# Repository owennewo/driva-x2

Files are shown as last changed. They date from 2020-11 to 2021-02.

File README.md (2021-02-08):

# driva-x2
Experimental dual BLDC board for use with [SimpleFOC](https://simplefoc.com)

This board will cost about $200 for 5 units from JLCPCB. Include are [gerber zip](https://github.com/owennewo/driva-x2/blob/main/kicad/gerber/driva-x2.zip), [BOM](https://github.com/owennewo/driva-x2/blob/main/kicad/assembly/driva-x2-bom.csv) and [POS](https://github.com/owennewo/driva-x2/blob/main/kicad/assembly/driva-x2-all-pos.csv).  Designed in Kicad.  This is pre-alpha quality e.g. I'm uncertain how much of it will work.  I've tested v0.5 with motor and hall sensors on left motor and that worked.

 - dual motor drivers using 3x btn8982 or ixf0007s
 - each motor has hall and spi port (untested)
 - prog (swd, swdio), can (untested), usart and i2c (untested) ports
 - ubg-otg (utested and without 5v attached)
 - onboard mpu6050 for 6 axis imu

Note JLCPCB won't do through hole components therefore all power, motor, comms ports will need to be hand solder as will the 1000uF cap.  

The BOM and Pick/Place/POS file are here:
https://github.com/owennewo/driva-x2/tree/main/kicad/assembly 

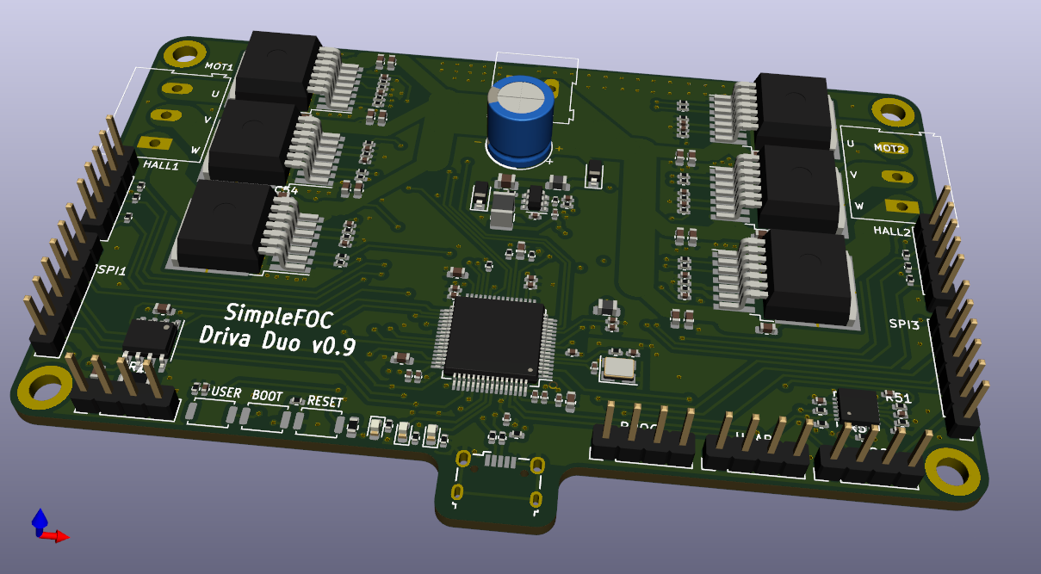
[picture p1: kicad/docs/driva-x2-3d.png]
3D render


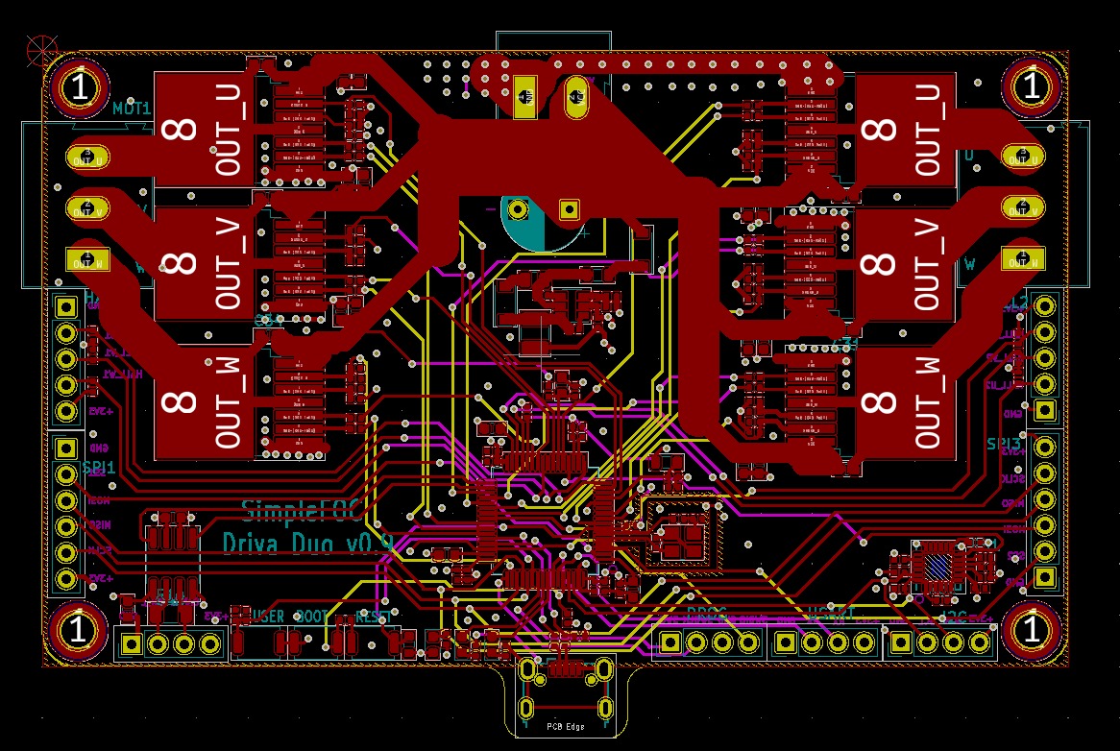
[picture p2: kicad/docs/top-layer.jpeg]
Top Layer


[PDF Schematic](./kicad/docs/driva-x2.pdf)

The gerber files are here:
https://github.com/owennewo/driva-x2/tree/main/kicad/gerber

The BOM and Pick/Place/POS file are here:
https://github.com/owennewo/driva-x2/tree/main/kicad/assembly

 * v0.5 - First attempt (partly working - problems with mpu6050, can and LDO)
 * v0.9 - Second attempt (fixed above hopefully - awaiting order from JLCPCB)

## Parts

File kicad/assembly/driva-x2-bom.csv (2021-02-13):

Id | Designator | Footprint | Quantity | Designation | LCSC Part Number
2 | C56,C54,C51,C49,C46,C44,C38,C36,C33,C31,C28,C26 | 0603 | 12 | 220n+ | C21120
3 | C55,C50,C45,C37,C32,C27 | 0603 | 6 | 100n+ | C14663
4 | R52,R51,R12,R13,R17,R21,R22,R25,R26,R29,R30,R33,R34,R37,R38,R41,R42 | 0402 | 17 | 10k | C25744
5 | R14 | 1206 | 1 | 120R+ | C22107
7 | R11 | 0603 | 1 | 2K2 | C4190
10 | C11,C2,C3,C4,C5,C6,C7,C8,C9,C10,C14,C18,C20,C25,C30,C35,C40,C41,C42,C48,C53,C58,C21 | 0402 | 23 | 100n | C1525
11 | C59 | 0402 | 1 | 33p | C1562
12 | C12 | 0402 | 1 | 10u | C15525
13 | U1 | SOT-23-6L | 1 | mp2451dt | C14123
14 | R50 | 0402 | 1 | 39k | C25783
15 | R49 | 0402 | 1 | 120k | C25750
16 | R48,R47,R46 | 0402 | 3 | 4.7k | C25900
17 | R45 | 0402 | 1 | 300K | C25774
18 | L1 | 1210 | 1 | 2.2uh | C86074
21 | D5,D1 | SOD-123 | 2 | b5819w | C8598
22 | C61,C15 | 0402 | 2 | 10n | C15195
23 | C13 | 0805 | 1 | 4.7u+ | C1779
24 | C1,C24 | 0603 | 2 | 10u | C19702
25 | C16,C17 | 0402 | 2 | 12p | C1547
26 | C19,C22,C23 | 0603 | 3 | 2.2u | C23630
27 | C29,C34,C39,C47,C52,C57 | 0402 | 6 | 1n | C1523
28 | C43 | 0402 | 1 | 2.2n | C1531
29 | D2 | LED_0603 | 1 | RED | C2286
30 | D3 | LED_0603 | 1 | GREEN | C72043
31 | D4 | LED_0603 | 1 | BLUE | C72041
32 | FB1,FB2 | 0805 | 2 | 100 @ 100Mhz | C1015
33 | HSE1 | SMD-CRY-3225_4P | 1 | 16MHz | C13738
42 | R1,R2,R3 | 0402 | 3 | 22R | C25092
43 | R4,R5,R6,R7,R8,R9 | 0402 | 6 | 1K5 | C25867
44 | R10 | 0402 | 1 | 220 | C25091
45 | R15 | 0402 | 1 | 33K | C25779
46 | R16 | 0402 | 1 | 3K3 | C25890
48 | R18,R19,R20,R23,R27,R31,R35,R39,R43 | 0402 | 9 | 1k | C11702
49 | R24,R28,R32,R36,R40,R44 | 0402 | 6 | 510R | C25123
50 | SW1,SW2,SW3 | SW-SMD-2_3.0x4.0x1.7 | 3 | push | C561519
51 | U2 | SOIC-8_3.9x4.9x1.27P | 1 | SN65HVD230 | C12084
52 | U3 | LQFP-64_10.0x10.0x0.5P | 1 | STM32F405RGTx | C15742
53 | U4,U5,U6,U8,U9,U10 | TO-263-7L | 6 | IFX007T | C74175
54 | U7 | QFN-24_EP_4.0x4.0x0.5P | 1 | MPU-6050 | C24112

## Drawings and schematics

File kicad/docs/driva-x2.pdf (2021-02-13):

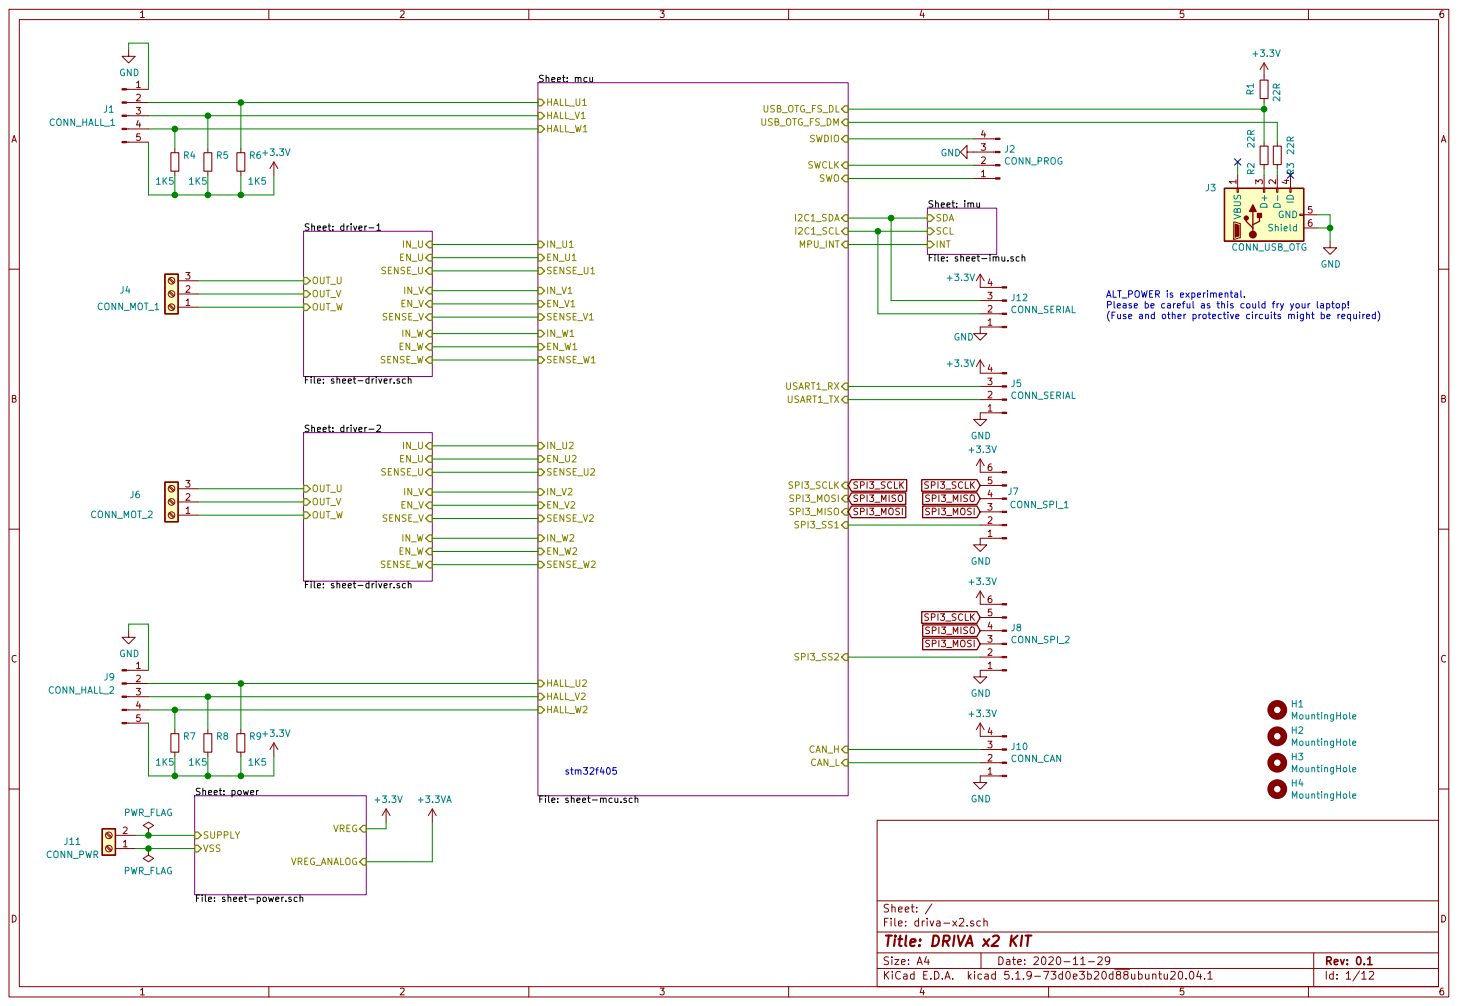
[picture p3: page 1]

Sheet: imu File: sheet-imu.sch SDA

INT Sheet: driver-1 File: sheet-driver.schSENSE_W

ALT_POWER is experimental.
Please be careful as this could fry your laptop!
(Fuse and other protective circuits might be required)
J10 CONN_CAN GND123456

Sheet: driver-2 File: sheet-driver.schSENSE_W

File: sheet-mcu.sch

File: sheet-power.sch VSS

File: driva-x2.sch Sheet: /
Id: 1/12 Title: DRIVA x2 KIT

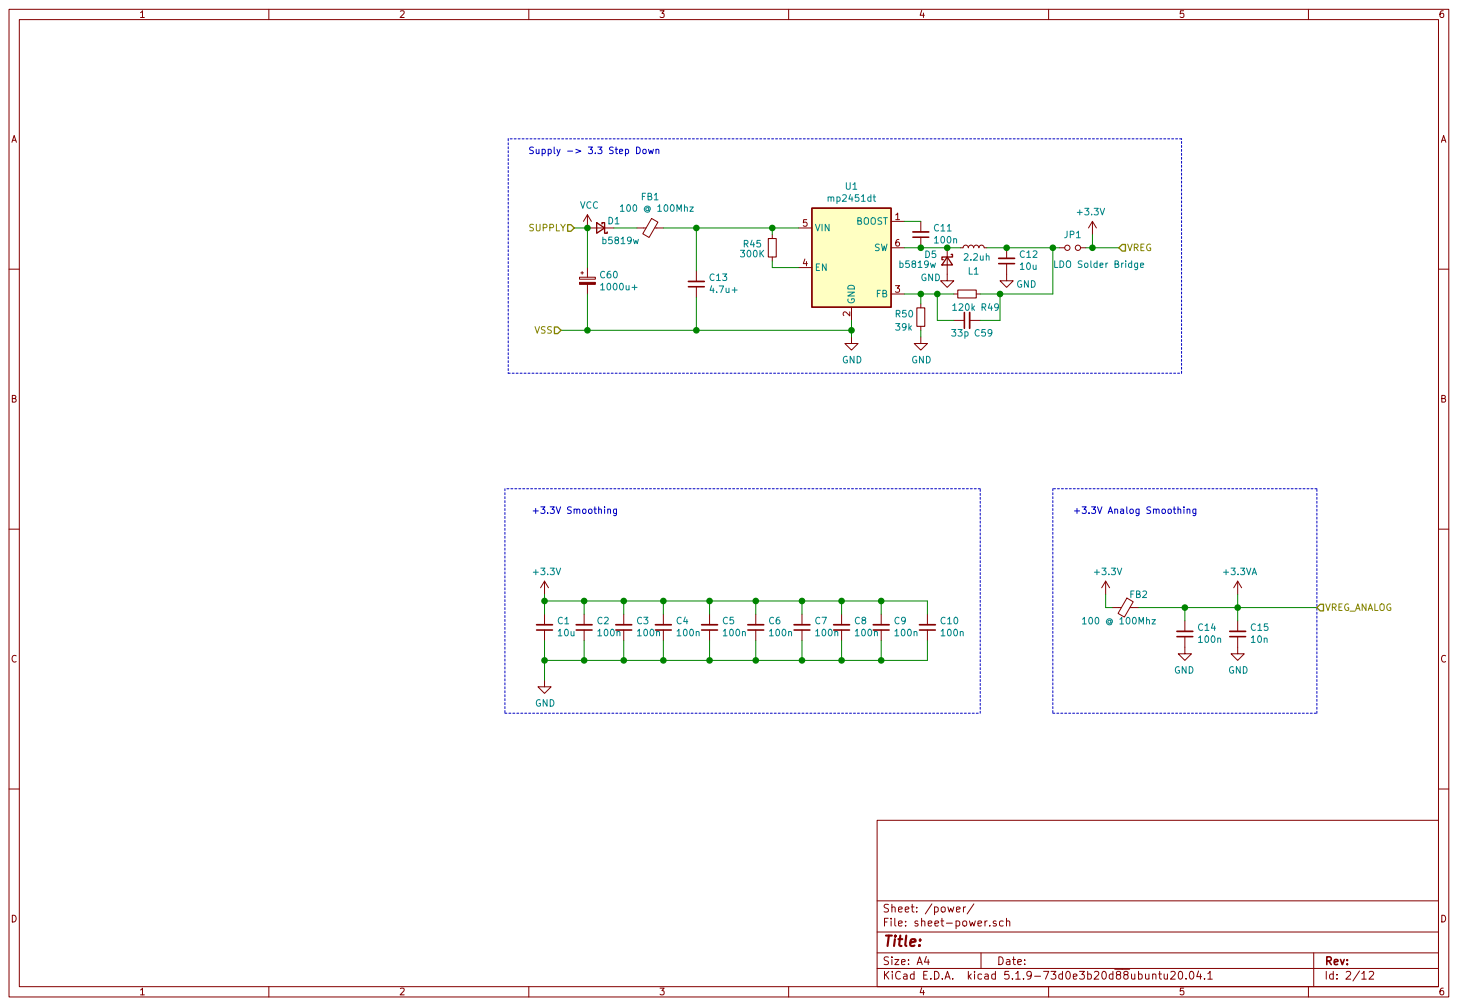
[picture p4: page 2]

2 FB 3 EN 4 VIN 5 SW 6 U1 mp2451dt GND GND

Sheet: /power/
File: sheet-power.sch
Id: 2/12 Title:

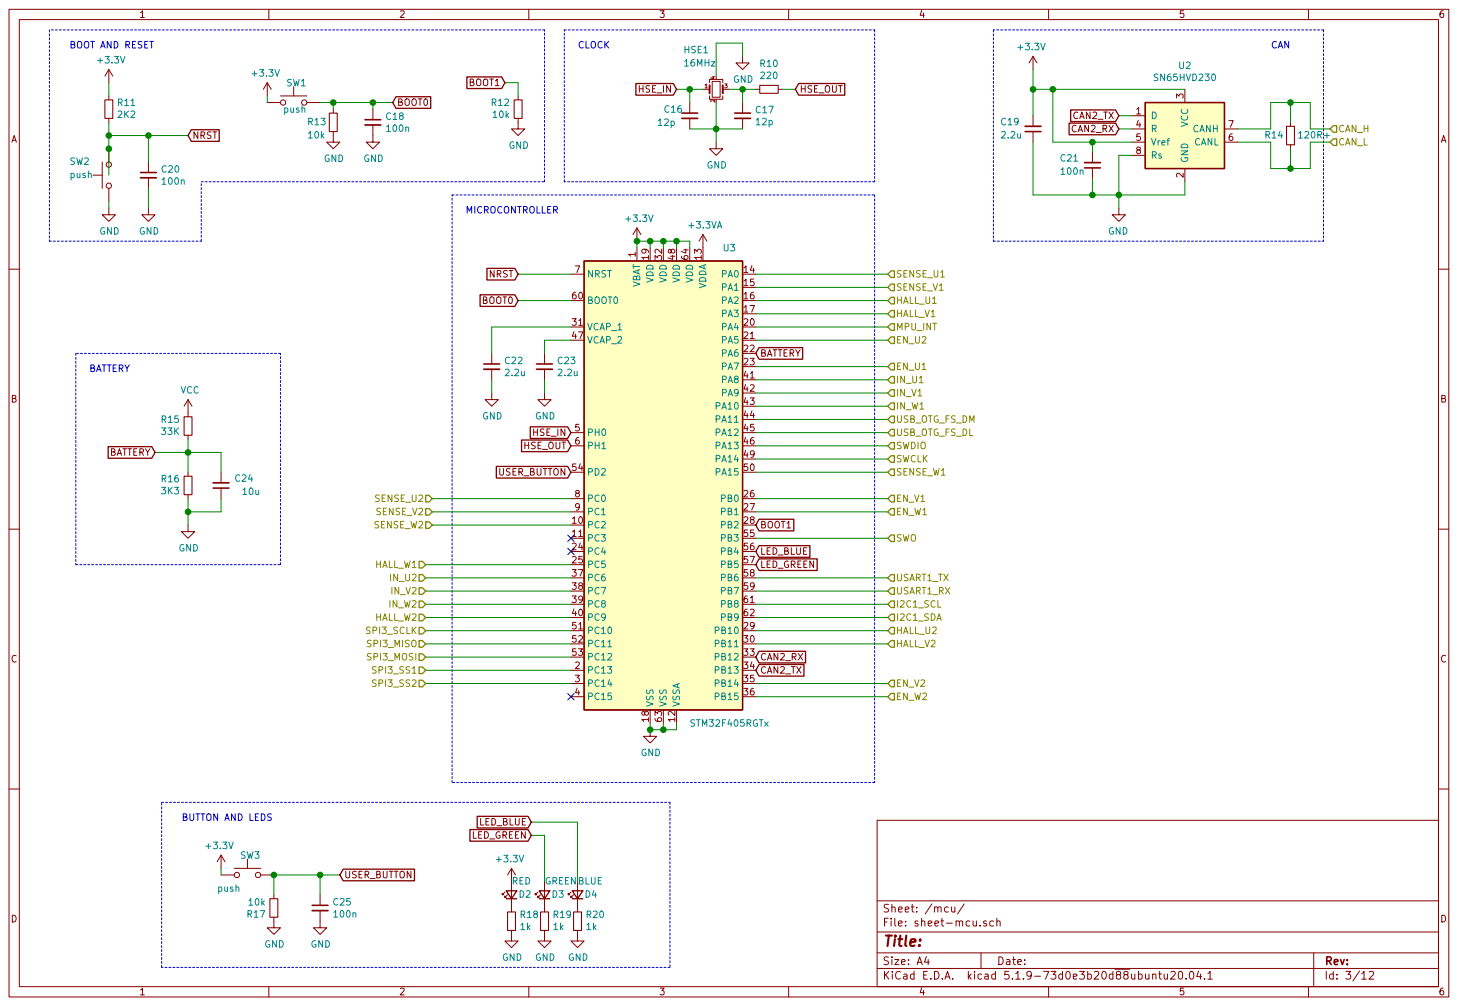
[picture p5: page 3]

1 VCAP_1 31 VCAP_2 47 VDD 19 VDD 32 VDD 48 VDD 64 VDDA 13 VSS 18 VSS 63 VSSA 12 U3 STM32F405RGTx

Id: 3/12 Title: File: sheet-mcu.sch Sheet: /mcu/ GND
1k GND

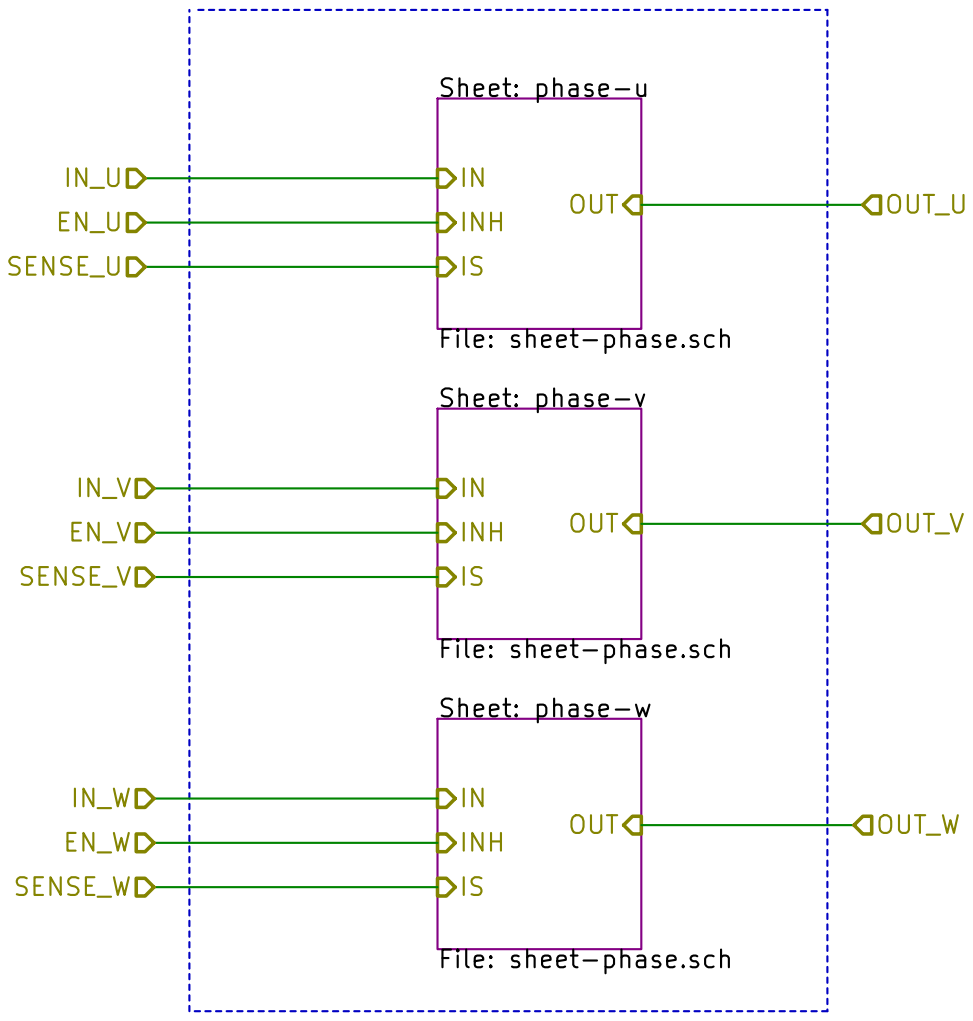
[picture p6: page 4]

File: sheet-phase.sch OUT
INH

Id: 4/12 Title: Driver File: sheet-driver.sch Sheet: /driver-2/ Root Top level

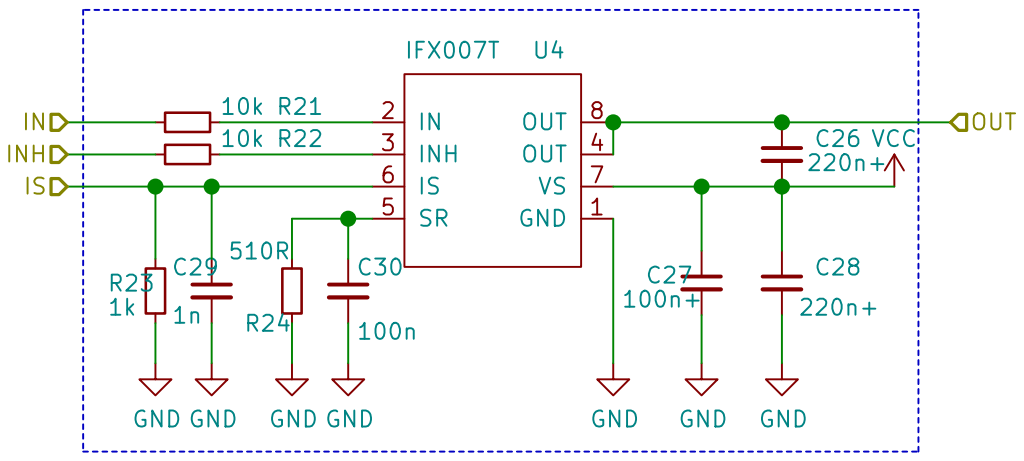
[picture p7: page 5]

File: sheet-phase.sch
Id: 5/12 Title:

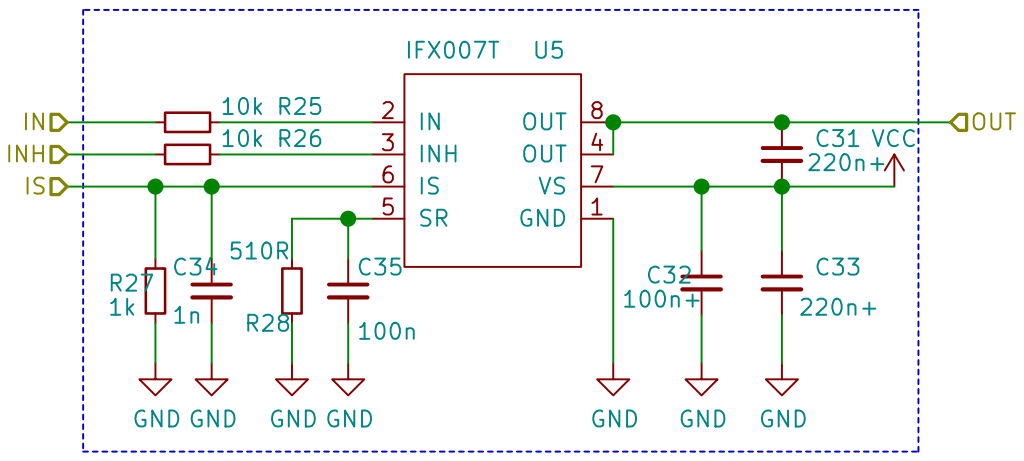
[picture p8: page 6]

File: sheet-phase.sch
Id: 6/12 Title:

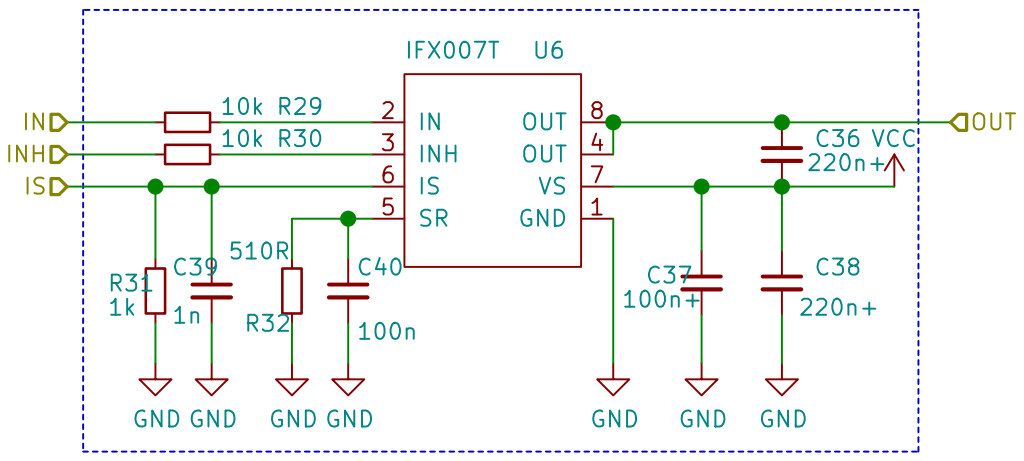
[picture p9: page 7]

File: sheet-phase.sch
Id: 7/12 Title:

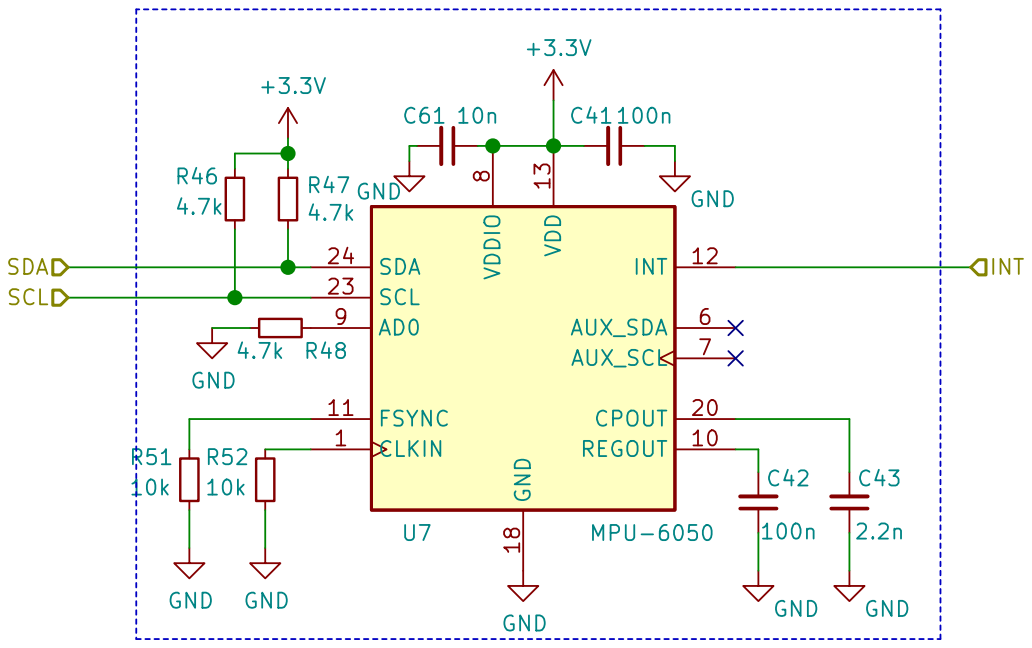
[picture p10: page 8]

Id: 8/12 Title: File: sheet-imu.sch Sheet: /imu/

File: sheet-phase.sch OUT
INH

Id: 9/12 Title: Driver File: sheet-driver.sch Sheet: /driver-1/ Root Top level

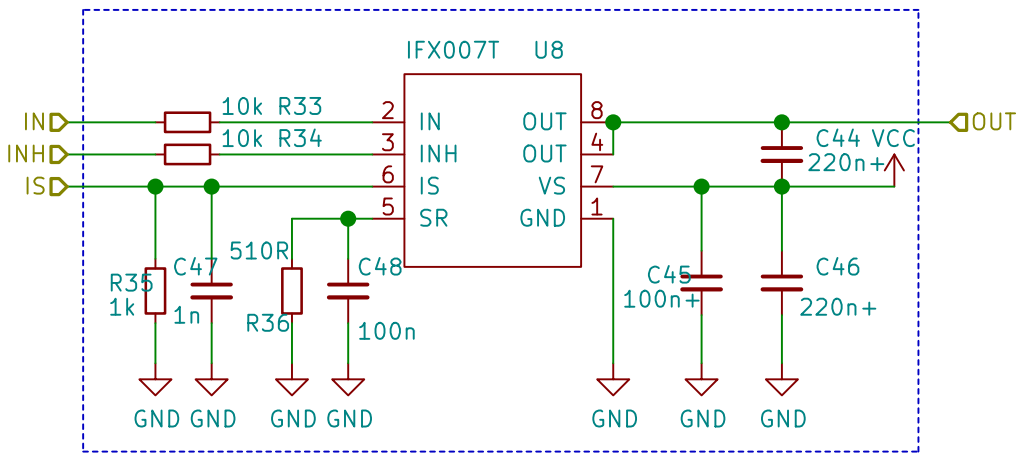
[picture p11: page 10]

File: sheet-phase.sch
Id: 10/12 Title:

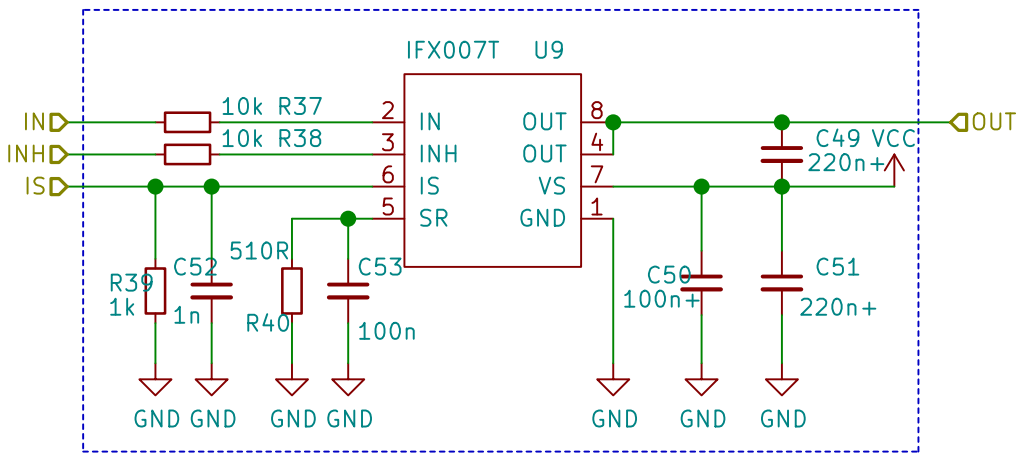
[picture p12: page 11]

File: sheet-phase.sch
Id: 11/12 Title:

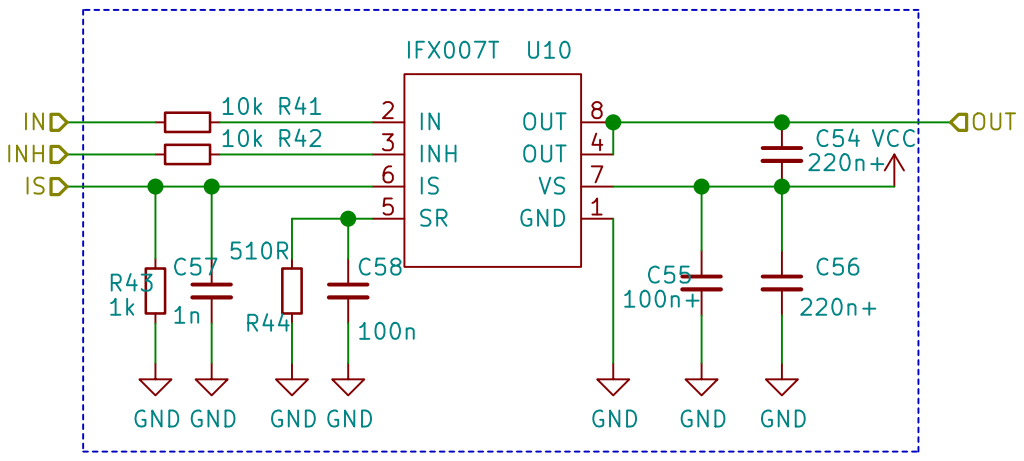
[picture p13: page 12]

File: sheet-phase.sch
Id: 12/12 Title:

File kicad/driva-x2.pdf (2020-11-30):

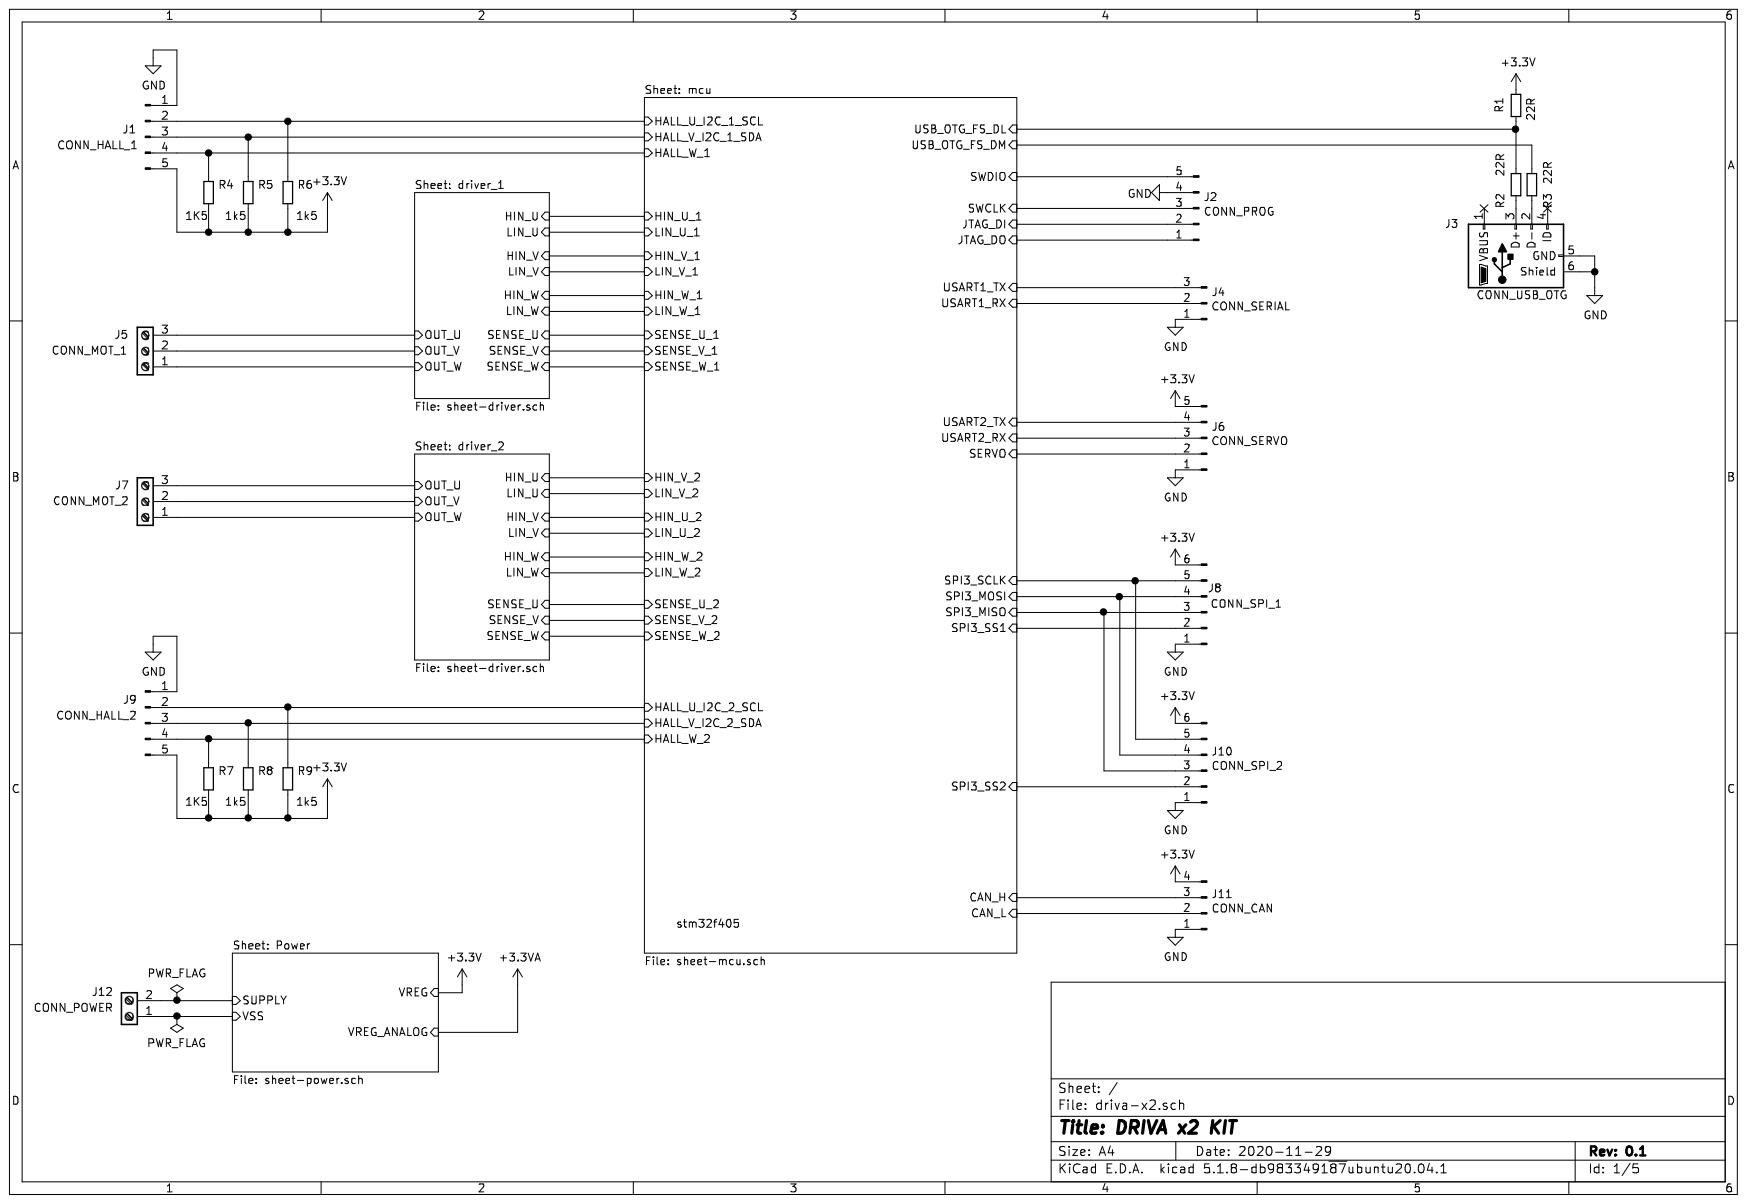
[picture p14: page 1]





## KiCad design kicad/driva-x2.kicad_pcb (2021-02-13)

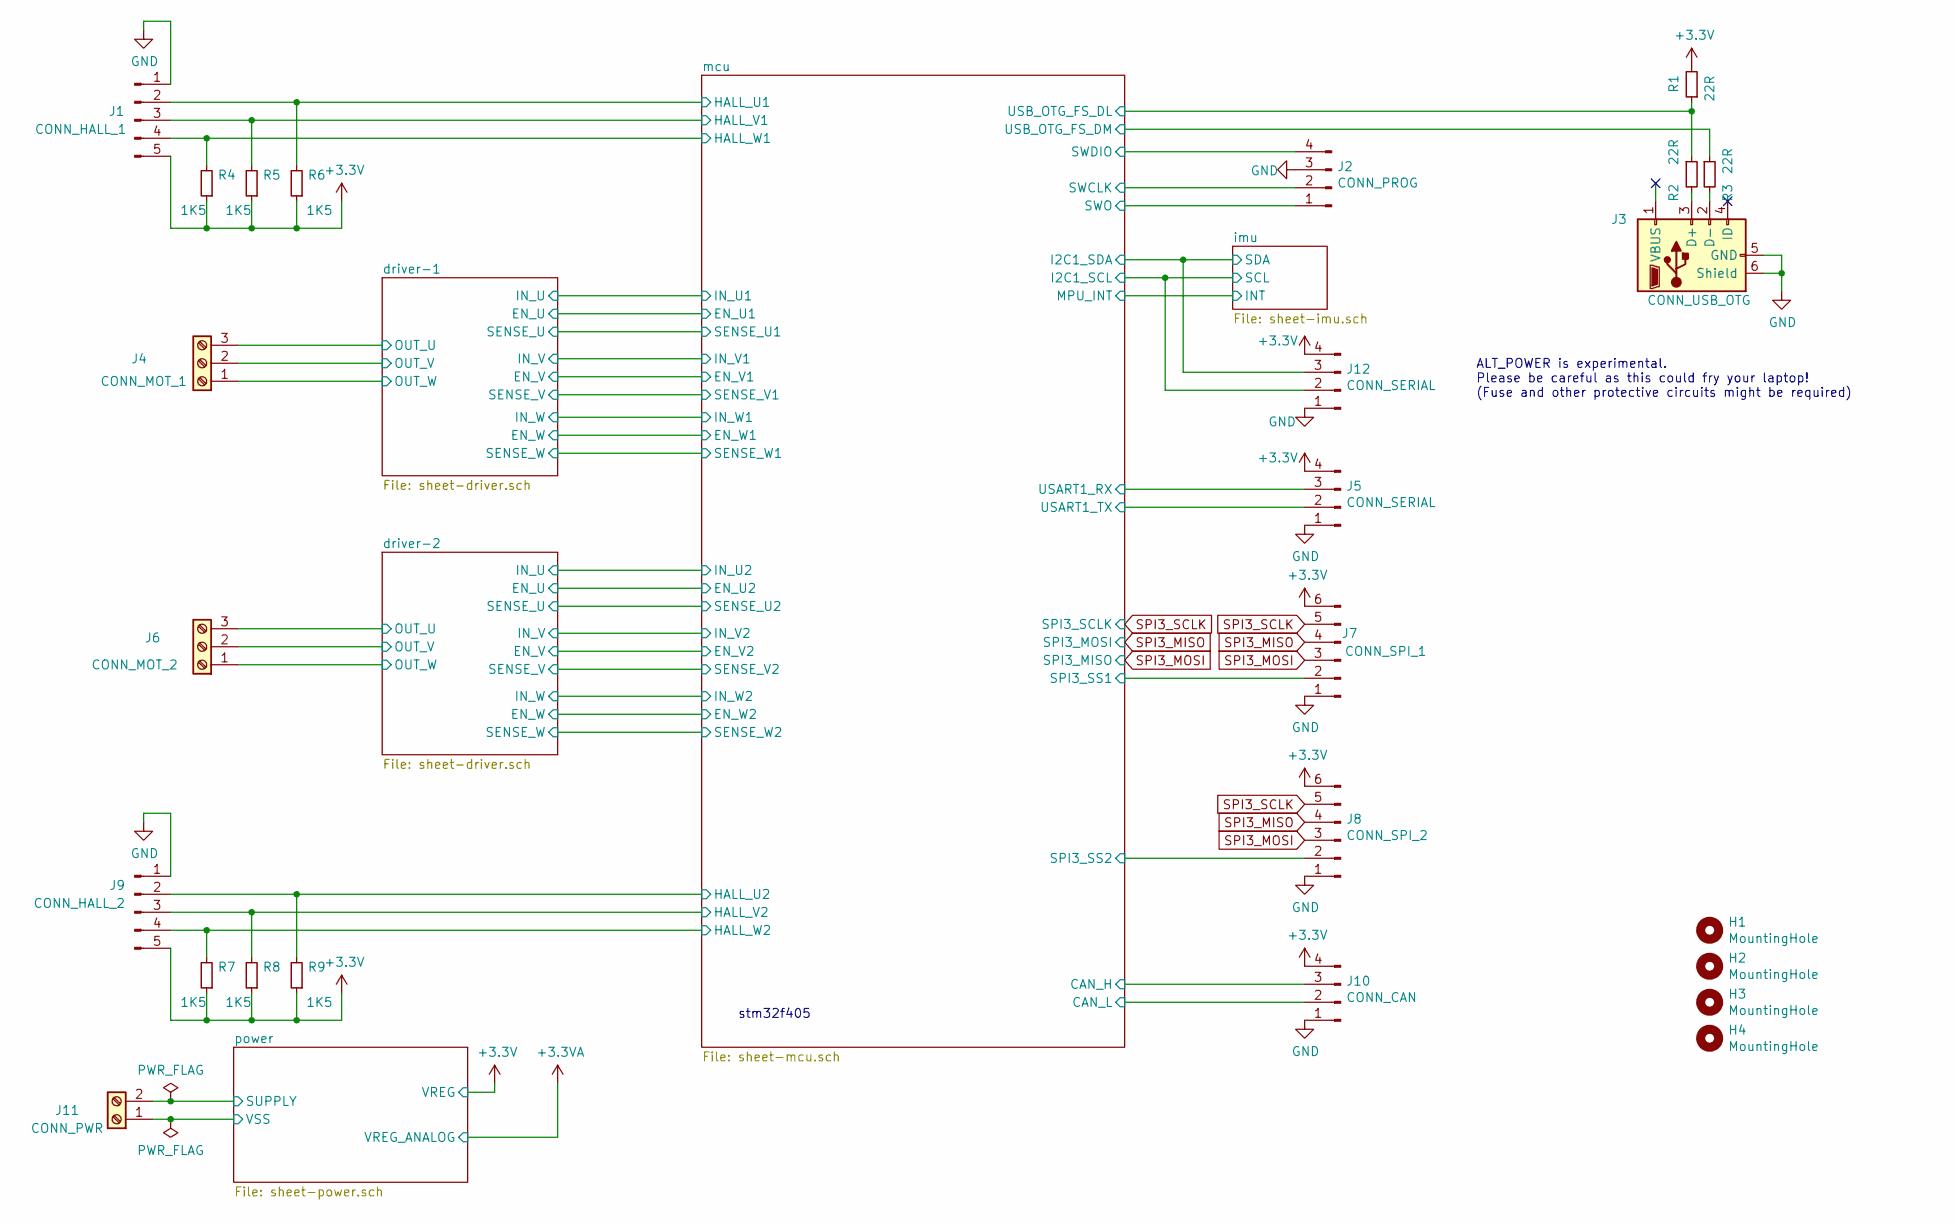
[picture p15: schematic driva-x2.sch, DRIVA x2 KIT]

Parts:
H1, H2, H3, H4: MountingHole; MountingHole_3.2mm_M3_ISO14580_Pad_TopBottom
J1: CONN_HALL_1; PinHeader_1x05_P2.54mm_Vertical
J2: CONN_PROG; PinHeader_1x04_P2.54mm_Vertical
J3: CONN_USB_OTG; USB_Micro-B_Wuerth_629105150521
J4: CONN_MOT_1; TerminalBlock_Altech_AK300-3_P5.00mm
J5, J12: CONN_SERIAL; PinHeader_1x04_P2.54mm_Vertical
J6: CONN_MOT_2; TerminalBlock_Altech_AK300-3_P5.00mm
J7: CONN_SPI_1; PinHeader_1x06_P2.54mm_Vertical
J8: CONN_SPI_2; PinHeader_1x06_P2.54mm_Vertical
J9: CONN_HALL_2; PinHeader_1x05_P2.54mm_Vertical
J10: CONN_CAN; PinHeader_1x04_P2.54mm_Vertical
J11: CONN_PWR; TerminalBlock_Altech_AK300-2_P5.00mm
R1, R2, R3: 22R; R_0402_1005Metric
R4, R5, R6, R7, R8, R9: 1K5; R_0402_1005Metric

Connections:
+3V3: J1.5, J5.4, J7.6, J8.6, J9.5, J10.4, J12.4, R1.2, R4.1, R5.1, R6.1, R7.1, R8.1, R9.1; also elsewhere on the board
/driver-1/OUT_U: J4.3; also elsewhere on the board
/driver-1/OUT_V: J4.2; also elsewhere on the board
/driver-1/OUT_W: J4.1; also elsewhere on the board
/driver-2/OUT_U: J6.3; also elsewhere on the board
/driver-2/OUT_V: J6.2; also elsewhere on the board
/driver-2/OUT_W: J6.1; also elsewhere on the board
/mcu/CAN_H: J10.3; also elsewhere on the board
/mcu/CAN_L: J10.2; also elsewhere on the board
/mcu/HALL_U1: J1.2, R6.2; also elsewhere on the board
/mcu/HALL_U2: J9.2, R9.2; also elsewhere on the board
/mcu/HALL_V1: J1.3, R5.2; also elsewhere on the board
/mcu/HALL_V2: J9.3, R8.2; also elsewhere on the board
/mcu/HALL_W1: J1.4, R4.2; also elsewhere on the board
/mcu/HALL_W2: J9.4, R7.2; also elsewhere on the board
/mcu/I2C1_SCL: J12.2; also elsewhere on the board
/mcu/I2C1_SDA: J12.3; also elsewhere on the board
/mcu/SPI3_SS1: J7.2; also elsewhere on the board
/mcu/SPI3_SS2: J8.2; also elsewhere on the board
/mcu/SWCLK: J2.2; also elsewhere on the board
/mcu/SWDIO: J2.4; also elsewhere on the board
/mcu/SWO: J2.1; also elsewhere on the board
/mcu/USART1_RX: J5.3; also elsewhere on the board
/mcu/USART1_TX: J5.2; also elsewhere on the board
/mcu/USB_OTG_FS_DL: R1.1, R2.1; also elsewhere on the board
/mcu/USB_OTG_FS_DM: R3.1; also elsewhere on the board
GND: J1.1, J2.3, J3.5 (GND), J3.6 (Shield), J5.1, J7.1, J8.1, J9.1, J10.1, J11.1, J12.1; also elsewhere on the board
unnamed: J3.2 (D-), R3.2
unnamed: J3.3 (D+), R2.2
SPI3_MISO: J7.4, J8.4; also elsewhere on the board
SPI3_MOSI: J7.3, J8.3; also elsewhere on the board
SPI3_SCLK: J7.5, J8.5; also elsewhere on the board
VCC: J11.2; also elsewhere on the board

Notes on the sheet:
stm32f405
ALT_POWER is experimental. Please be careful as this could fry your laptop! (Fuse and other protective circuits might be required)

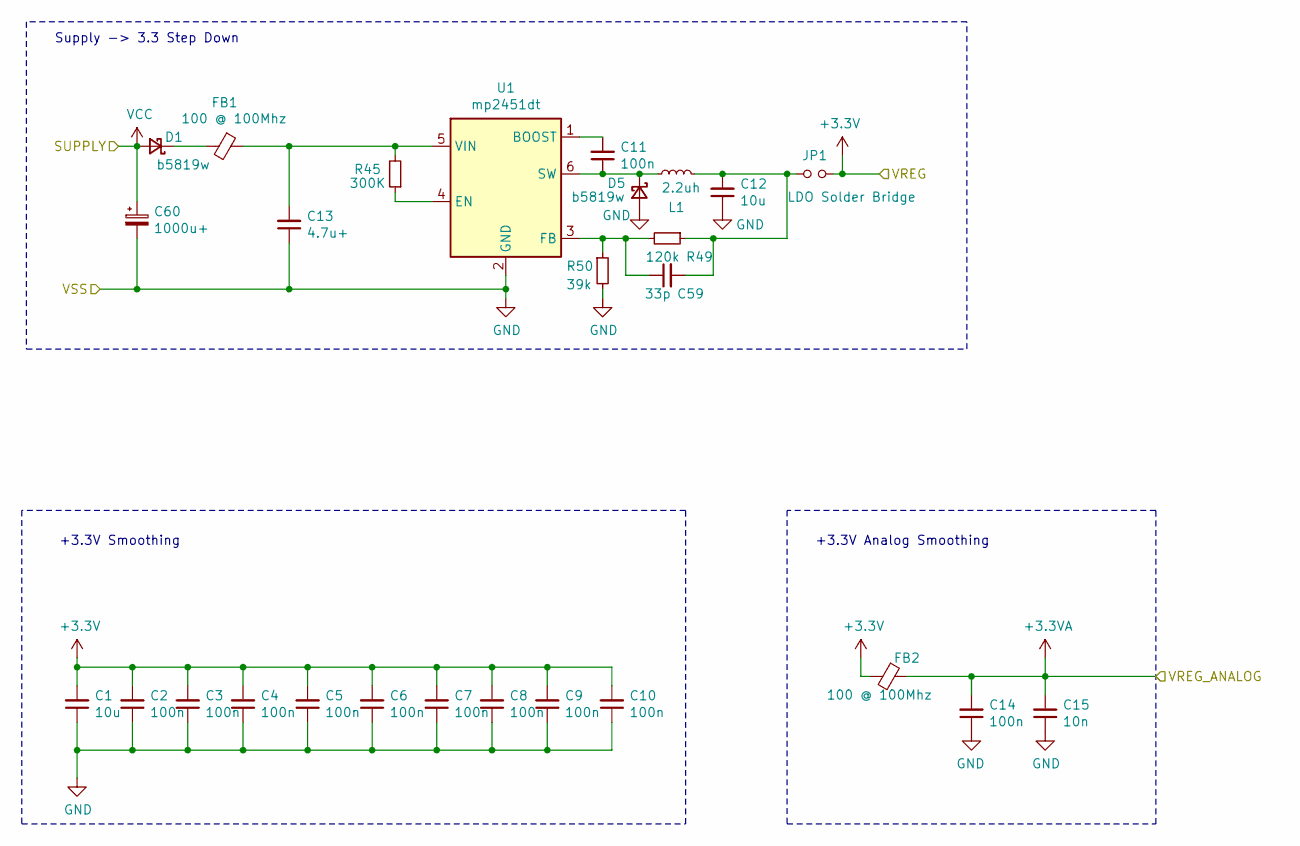
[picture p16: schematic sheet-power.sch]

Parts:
C1: 10u; C_0603_1608Metric
C2, C3, C4, C5, C6, C7, C8, C9, C10, C11, C14: 100n; C_0402_1005Metric
C12: 10u; C_0402_1005Metric
C13: 4.7u+; C_0805_2012Metric
C15: 10n; C_0402_1005Metric
C59: 33p; C_0402_1005Metric
C60: 1000u+; CP_Radial_D8.0mm_P5.00mm
D1, D5: b5819w; D_SOD-123
FB1, FB2: 100 @ 100Mhz; L_0805_2012Metric
JP1: LDO Solder Bridge; SolderJumper-2_P1.3mm_Bridged_Pad1.0x1.5mm
L1: 2.2uh; L_1210_3225Metric
R45: 300K; R_0402_1005Metric
R49: 120k; R_0402_1005Metric
R50: 39k; R_0402_1005Metric
U1: mp2451dt; SOT-23-6

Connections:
+3.3VA: C14.2, C15.2, FB2.1; also elsewhere on the board
+3V3: C1.2, C2.2, C3.2, C4.2, C5.2, C6.2, C7.2, C8.2, C9.2, C10.2, FB2.2, JP1.2; also elsewhere on the board
GND: C1.1, C2.1, C3.1, C4.1, C5.1, C6.1, C7.1, C8.1, C9.1, C10.1, C12.1, C13.1, C14.1, C15.1, C60.2, D5.2 (A), R50.2, U1.2 (GND); also elsewhere on the board
unnamed: C11.1, D5.1 (K), L1.1, U1.6 (SW)
unnamed: C11.2, U1.1 (BOOST)
unnamed: C12.2, C59.2, JP1.1, L1.2, R49.1
unnamed: C13.2, FB1.1, R45.2, U1.5 (VIN)
unnamed: C59.1, R49.2, R50.1, U1.3 (FB)
unnamed: D1.1 (K), FB1.2
unnamed: R45.1, U1.4 (EN)
VCC: C60.1, D1.2 (A); also elsewhere on the board

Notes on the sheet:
+3.3V Smoothing
+3.3V Analog Smoothing
Supply -> 3.3 Step Down

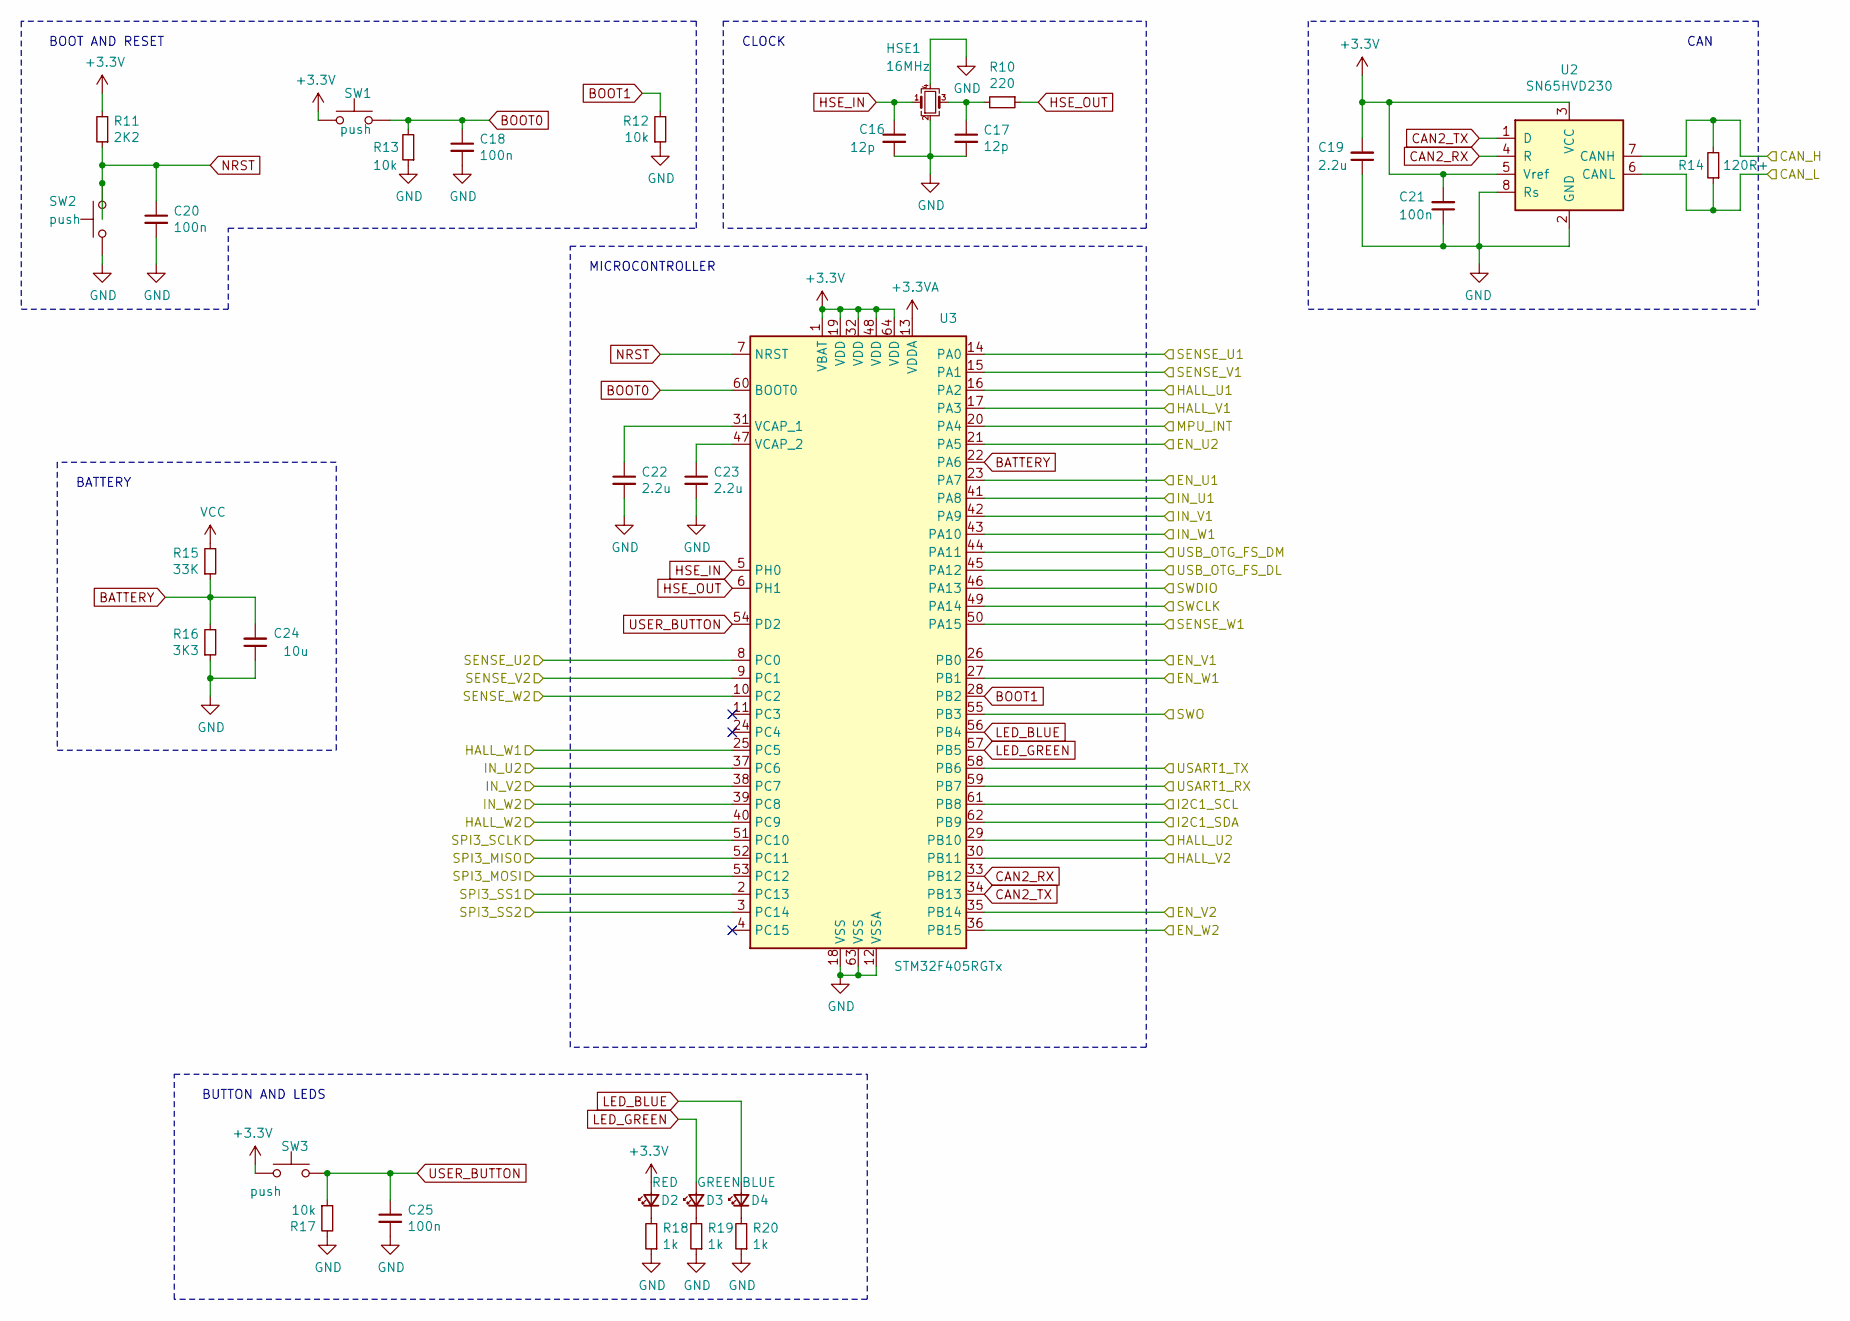
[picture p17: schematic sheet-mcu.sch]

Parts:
C16, C17: 12p; C_0402_1005Metric
C18, C20, C21, C25: 100n; C_0402_1005Metric
C19, C22, C23: 2.2u; C_0603_1608Metric
C24: 10u; C_0603_1608Metric
D2: RED; LED_0603_1608Metric
D3: GREEN; LED_0603_1608Metric
D4: BLUE; LED_0603_1608Metric
HSE1: 16MHz; Crystal_SMD_3225-4Pin_3.2x2.5mm
R10: 220; R_0402_1005Metric
R11: 2K2; R_0603_1608Metric
R12, R13, R17: 10k; R_0402_1005Metric
R14: 120R+; R_1206_3216Metric
R15: 33K; R_0402_1005Metric
R16: 3K3; R_0402_1005Metric
R18, R19, R20: 1k; R_0402_1005Metric
SW1, SW2, SW3: push; SW_Push_SPST_NO_Alps_SKRK
U2: SN65HVD230; SOIC-8_3.9x4.9mm_P1.27mm
U3: STM32F405RGTx; LQFP-64_10x10mm_P0.5mm

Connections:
+3.3VA: U3.13 (VDDA); also elsewhere on the board
+3V3: C19.2, C21.2, D2.2 (A), R11.2, SW1.1, SW3.1, U2.3 (VCC), U2.5 (Vref), U3.1 (VBAT), U3.19 (VDD), U3.32 (VDD), U3.48 (VDD), U3.64 (VDD); also elsewhere on the board
/driver-1/EN_U: U3.23 (PA7); also elsewhere on the board
/driver-1/EN_V: U3.26 (PB0); also elsewhere on the board
/driver-1/EN_W: U3.27 (PB1); also elsewhere on the board
/driver-1/IN_U: U3.41 (PA8); also elsewhere on the board
/driver-1/IN_V: U3.42 (PA9); also elsewhere on the board
/driver-1/IN_W: U3.43 (PA10); also elsewhere on the board
/driver-1/SENSE_U: U3.14 (PA0); also elsewhere on the board
/driver-1/SENSE_V: U3.15 (PA1); also elsewhere on the board
/driver-1/SENSE_W: U3.50 (PA15); also elsewhere on the board
/driver-2/EN_U: U3.21 (PA5); also elsewhere on the board
/driver-2/EN_V: U3.35 (PB14); also elsewhere on the board
/driver-2/EN_W: U3.36 (PB15); also elsewhere on the board
/driver-2/IN_U: U3.37 (PC6); also elsewhere on the board
/driver-2/IN_V: U3.38 (PC7); also elsewhere on the board
/driver-2/IN_W: U3.39 (PC8); also elsewhere on the board
/driver-2/SENSE_U: U3.8 (PC0); also elsewhere on the board
/driver-2/SENSE_V: U3.9 (PC1); also elsewhere on the board
/driver-2/SENSE_W: U3.10 (PC2); also elsewhere on the board
/imu/INT: U3.20 (PA4); also elsewhere on the board
/mcu/CAN_H: R14.2, U2.7 (CANH); also elsewhere on the board
/mcu/CAN_L: R14.1, U2.6 (CANL); also elsewhere on the board
/mcu/HALL_U1: U3.16 (PA2); also elsewhere on the board
/mcu/HALL_U2: U3.29 (PB10); also elsewhere on the board
/mcu/HALL_V1: U3.17 (PA3); also elsewhere on the board
/mcu/HALL_V2: U3.30 (PB11); also elsewhere on the board
/mcu/HALL_W1: U3.25 (PC5); also elsewhere on the board
/mcu/HALL_W2: U3.40 (PC9); also elsewhere on the board
/mcu/I2C1_SCL: U3.61 (PB8); also elsewhere on the board
/mcu/I2C1_SDA: U3.62 (PB9); also elsewhere on the board
/mcu/SPI3_SS1: U3.2 (PC13); also elsewhere on the board
/mcu/SPI3_SS2: U3.3 (PC14); also elsewhere on the board
/mcu/SWCLK: U3.49 (PA14); also elsewhere on the board
/mcu/SWDIO: U3.46 (PA13); also elsewhere on the board
/mcu/SWO: U3.55 (PB3); also elsewhere on the board
/mcu/USART1_RX: U3.59 (PB7); also elsewhere on the board
/mcu/USART1_TX: U3.58 (PB6); also elsewhere on the board
/mcu/USB_OTG_FS_DL: U3.45 (PA12); also elsewhere on the board
/mcu/USB_OTG_FS_DM: U3.44 (PA11); also elsewhere on the board
BATTERY: C24.2, R15.1, R16.2, U3.22 (PA6)
BOOT0: C18.1, R13.2, SW1.2, U3.60 (BOOT0)
BOOT1: R12.2, U3.28 (PB2)
CAN2_RX: U2.4 (R), U3.33 (PB12)
CAN2_TX: U2.1 (D), U3.34 (PB13)
GND: C16.2, C17.2, C18.2, C19.1, C20.2, C21.1, C22.2, C23.2, C24.1, C25.2, HSE1.2, HSE1.4, R12.1, R13.1, R16.1, R17.2, R18.1, R19.1, R20.1, SW2.1, U2.2 (GND), U2.8 (Rs), U3.12 (VSSA), U3.18 (VSS), U3.63 (VSS); also elsewhere on the board
HSE_IN: C16.1, HSE1.1, U3.5 (PH0)
HSE_OUT: R10.1, U3.6 (PH1)
LED_BLUE: D4.2 (A), U3.56 (PB4)
LED_GREEN: D3.2 (A), U3.57 (PB5)
NRST: C20.1, R11.1, SW2.2, U3.7 (NRST)
unnamed: C17.1, HSE1.3, R10.2
unnamed: C22.1, U3.31 (VCAP_1)
unnamed: C23.1, U3.47 (VCAP_2)
unnamed: D2.1 (K), R18.2
unnamed: D3.1 (K), R19.2
unnamed: D4.1 (K), R20.2
SPI3_MISO: U3.53 (PC12); also elsewhere on the board
SPI3_MOSI: U3.52 (PC11); also elsewhere on the board
SPI3_SCLK: U3.51 (PC10); also elsewhere on the board
USER_BUTTON: C25.1, R17.1, SW3.2, U3.54 (PD2)
VCC: R15.2; also elsewhere on the board

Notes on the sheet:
MICROCONTROLLER
BOOT AND RESET
CLOCK
CAN
BATTERY
BUTTON AND LEDS

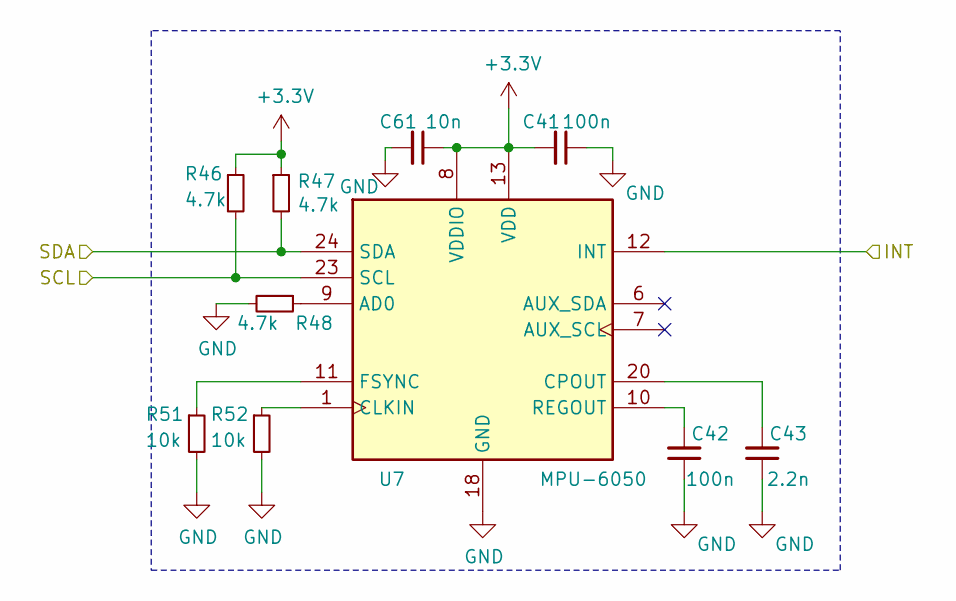
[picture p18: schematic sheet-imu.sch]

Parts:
C41, C42: 100n; C_0402_1005Metric
C43: 2.2n; C_0402_1005Metric
C61: 10n; C_0402_1005Metric
R46, R47, R48: 4.7k; R_0402_1005Metric
R51, R52: 10k; R_0402_1005Metric
U7: MPU-6050; InvenSense_QFN-24_4x4mm_P0.5mm

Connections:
+3V3: C41.2, C61.1, R46.1, R47.1, U7.8 (VDDIO), U7.13 (VDD); also elsewhere on the board
/imu/INT: U7.12 (INT); also elsewhere on the board
/mcu/I2C1_SCL: R46.2, U7.23 (SCL); also elsewhere on the board
/mcu/I2C1_SDA: R47.2, U7.24 (SDA); also elsewhere on the board
GND: C41.1, C42.1, C43.1, C61.2, R48.2, R51.2, R52.2, U7.18 (GND); also elsewhere on the board
unnamed: C42.2, U7.10 (REGOUT)
unnamed: C43.2, U7.20 (CPOUT)
unnamed: R48.1, U7.9 (AD0)
unnamed: R51.1, U7.11 (FSYNC)
unnamed: R52.1, U7.1 (CLKIN)

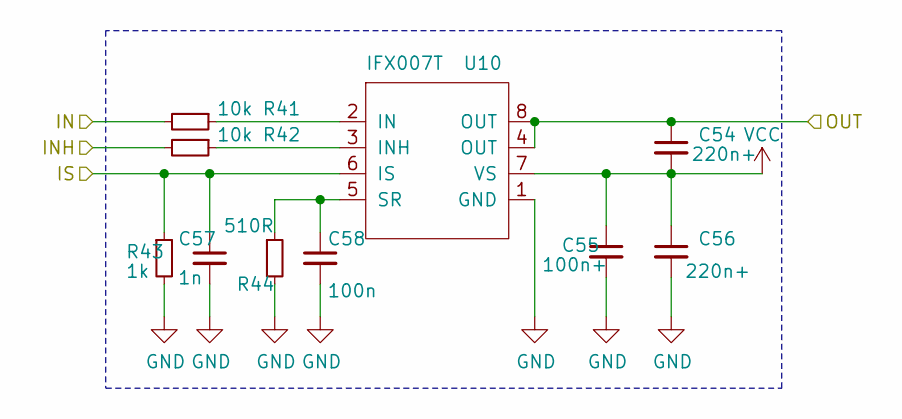
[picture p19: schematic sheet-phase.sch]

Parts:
C44, C46: 220n+; C_0603_1608Metric
C45: 100n+; C_0603_1608Metric
C47: 1n; C_0402_1005Metric
C48: 100n; C_0402_1005Metric
R33, R34: 10k; R_0402_1005Metric
R35: 1k; R_0402_1005Metric
R36: 510R; R_0402_1005Metric
U8: IFX007T; TO-263-7_TabPin8

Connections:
/driver-1/EN_U: R34.2; also elsewhere on the board
/driver-1/IN_U: R33.2; also elsewhere on the board
/driver-1/OUT_U: C44.1, U8.4 (OUT), U8.8 (OUT); also elsewhere on the board
/driver-1/SENSE_U: C47.1, R35.1, U8.6 (IS); also elsewhere on the board
GND: C45.2, C46.2, C47.2, C48.2, R35.2, R36.2, U8.1 (GND); also elsewhere on the board
unnamed: C48.1, R36.1, U8.5 (SR)
unnamed: R33.1, U8.2 (IN)
unnamed: R34.1, U8.3 (INH)
VCC: C44.2, C45.1, C46.1, U8.7 (VS); also elsewhere on the board

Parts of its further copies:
C26, C28, C31, C33, C36, C38, C49, C51, C54, C56: 220n+; C_0603_1608Metric
C27, C32, C37, C50, C55: 100n+; C_0603_1608Metric
C29, C34, C39, C52, C57: 1n; C_0402_1005Metric
C30, C35, C40, C53, C58: 100n; C_0402_1005Metric
R21, R22, R25, R26, R29, R30, R37, R38, R41, R42: 10k; R_0402_1005Metric
R23, R27, R31, R39, R43: 1k; R_0402_1005Metric
R24, R28, R32, R40, R44: 510R; R_0402_1005Metric
U4, U5, U6, U9, U10: IFX007T; TO-263-7_TabPin8

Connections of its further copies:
/driver-1/EN_V: R38.2; also elsewhere on the board
/driver-1/EN_W: R42.2; also elsewhere on the board
/driver-1/IN_V: R37.2; also elsewhere on the board
/driver-1/IN_W: R41.2; also elsewhere on the board
/driver-1/OUT_V: C49.1, U9.4 (OUT), U9.8 (OUT); also elsewhere on the board
/driver-1/OUT_W: C54.1, U10.4 (OUT), U10.8 (OUT); also elsewhere on the board
/driver-1/SENSE_V: C52.1, R39.1, U9.6 (IS); also elsewhere on the board
/driver-1/SENSE_W: C57.1, R43.1, U10.6 (IS); also elsewhere on the board
/driver-2/EN_U: R22.2; also elsewhere on the board
/driver-2/EN_V: R26.2; also elsewhere on the board
/driver-2/EN_W: R30.2; also elsewhere on the board
/driver-2/IN_U: R21.2; also elsewhere on the board
/driver-2/IN_V: R25.2; also elsewhere on the board
/driver-2/IN_W: R29.2; also elsewhere on the board
/driver-2/OUT_U: C26.1, U4.4 (OUT), U4.8 (OUT); also elsewhere on the board
/driver-2/OUT_V: C31.1, U5.4 (OUT), U5.8 (OUT); also elsewhere on the board
/driver-2/OUT_W: C36.1, U6.4 (OUT), U6.8 (OUT); also elsewhere on the board
/driver-2/SENSE_U: C29.1, R23.1, U4.6 (IS); also elsewhere on the board
/driver-2/SENSE_V: C34.1, R27.1, U5.6 (IS); also elsewhere on the board
/driver-2/SENSE_W: C39.1, R31.1, U6.6 (IS); also elsewhere on the board
GND: C27.2, C28.2, C29.2, C30.2, C32.2, C33.2, C34.2, C35.2, C37.2, C38.2, C39.2, C40.2, C50.2, C51.2, C52.2, C53.2, C55.2, C56.2, C57.2, C58.2, R23.2, R24.2, R27.2, R28.2, R31.2, R32.2, R39.2, R40.2, R43.2, R44.2, U4.1 (GND), U5.1 (GND), U6.1 (GND), U9.1 (GND), U10.1 (GND); also elsewhere on the board
unnamed: C30.1, R24.1, U4.5 (SR)
unnamed: C35.1, R28.1, U5.5 (SR)
unnamed: C40.1, R32.1, U6.5 (SR)
unnamed: C53.1, R40.1, U9.5 (SR)
unnamed: C58.1, R44.1, U10.5 (SR)
unnamed: R21.1, U4.2 (IN)
unnamed: R22.1, U4.3 (INH)
unnamed: R25.1, U5.2 (IN)
unnamed: R26.1, U5.3 (INH)
unnamed: R29.1, U6.2 (IN)
unnamed: R30.1, U6.3 (INH)
unnamed: R37.1, U9.2 (IN)
unnamed: R38.1, U9.3 (INH)
unnamed: R41.1, U10.2 (IN)
unnamed: R42.1, U10.3 (INH)
VCC: C26.2, C27.1, C28.1, C31.2, C32.1, C33.1, C36.2, C37.1, C38.1, C49.2, C50.1, C51.1, C54.2, C55.1, C56.1, U4.7 (VS), U5.7 (VS), U6.7 (VS), U9.7 (VS), U10.7 (VS); also elsewhere on the board

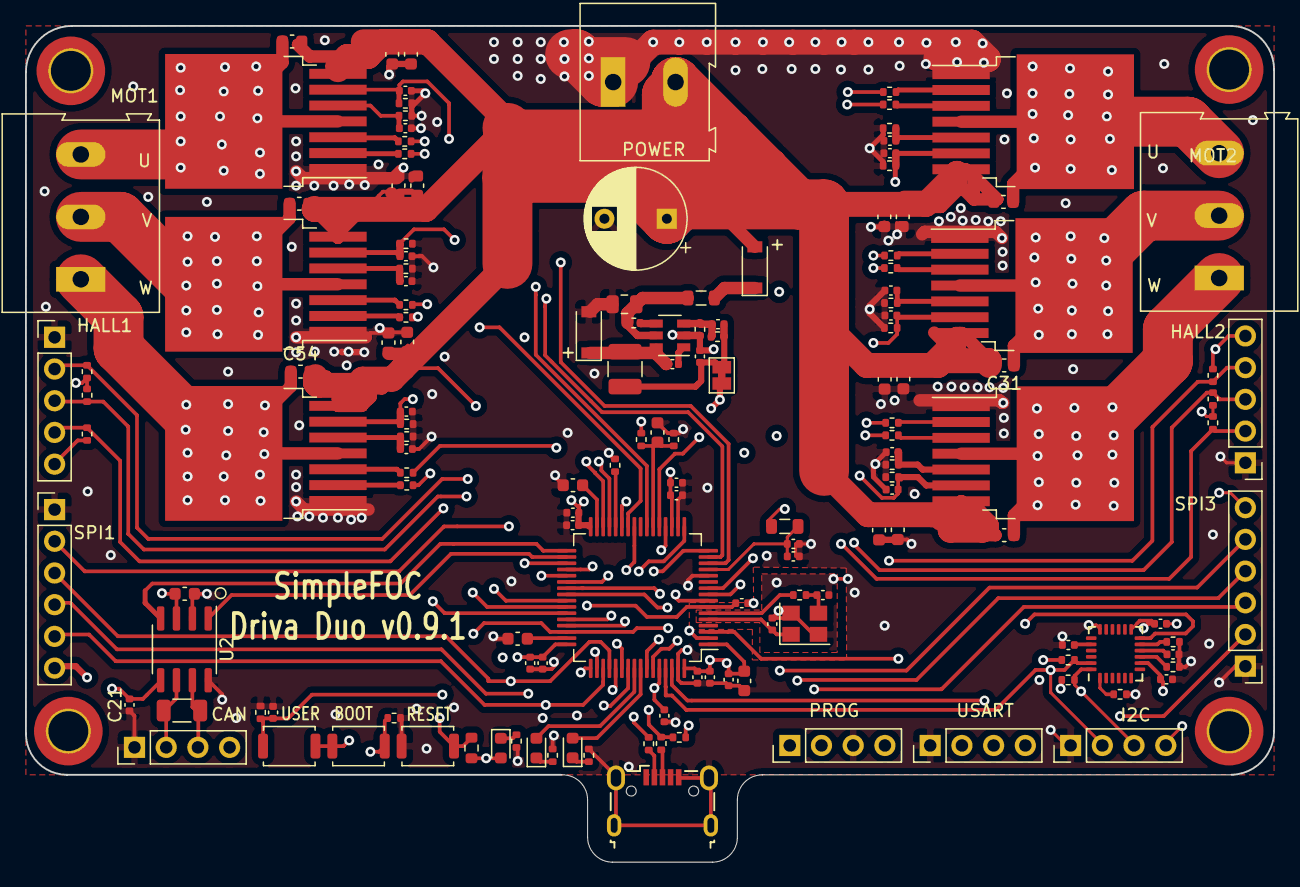
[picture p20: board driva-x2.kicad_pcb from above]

Board: 4 copper layers, 100.0 x 67.0 mm, 152 parts (0 on the bottom side), 100 nets.

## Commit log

2020-11-30 adding v0.1 of driva x3 kit
    [driva-x2.kicad_pcb, driva-x2.sch, driver.sch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]
2020-12-06 layout and bom complete - waiting on parts from jlcpcb
    [driva-x2-B_Cu.gbr, driva-x2-B_Mask.gbr, driva-x2-B_Paste.gbr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]
2021-02-05 Adding 0.9 version
    [driva-x2-B_Cu.gbr, driva-x2-B_Mask.gbr, driva-x2-B_Paste.gbr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]
2021-02-05 deleting old artefacts
    [driva-x2.csv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]
2021-02-07 adding solder bridge and more vias under driver
    [driva-x2.kicad_pcb, sheet-phase.sch, sheet-power.sch]
2021-02-08 updating bom and pos files
    [driva-x2-B_Cu.gbr, driva-x2-B_Mask.gbr, driva-x2-B_SilkS.gbr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]
2021-02-13 v0.9.1 swapping can to 3.3v SN65HVD230
    [driva-x2-B_Cu.gbr, driva-x2-B_Mask.gbr, driva-x2-B_SilkS.gbr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]
